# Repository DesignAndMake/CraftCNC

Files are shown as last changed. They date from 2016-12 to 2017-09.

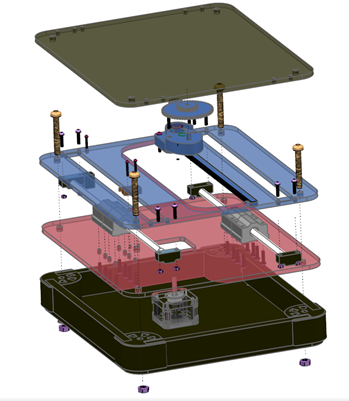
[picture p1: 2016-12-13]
CraftCNC_D1/Documentation/Assembly_Instructions/Images/Graphics/x axis 1.png

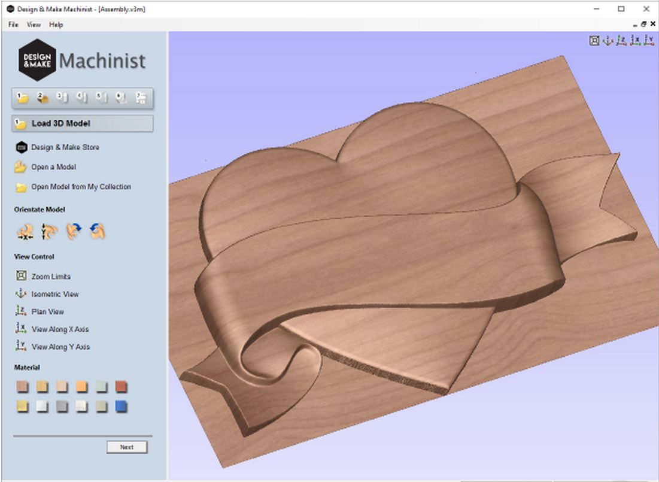
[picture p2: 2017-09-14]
CraftCNC_D1/Documentation/Assembly_Instructions/Images/Graphics/D&M Machinist.JPG

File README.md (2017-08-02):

## Welcome to the CraftCNC Wiki ##

If you want to build your own machine follow these steps:

* Download and print the STL files [STL files](https://github.com/DesignAndMake/CraftCNC/wiki/STL-files)
* Download and laser cut the DXF files [DXF files](https://github.com/DesignAndMake/CraftCNC/wiki/DXF-files-10mm)
* Follow the [Assembly Instructions](https://github.com/DesignAndMake/CraftCNC/wiki/Assembly-Instructions)
* Download and install the control software
* Grab a project from [Design & Make](https://www.designandmake.com)
* Your off!

## Self-build CNC

Self-build CNC (https://youtu.be/Zaxm20WJti4)

...more projects to follow

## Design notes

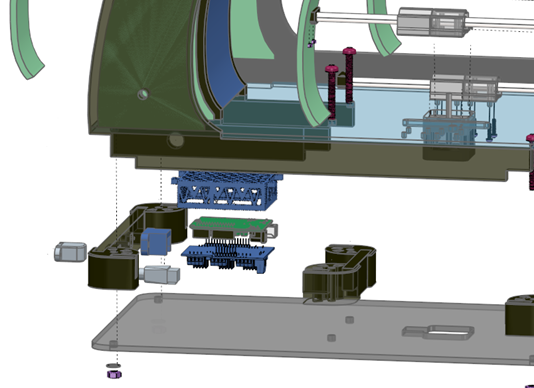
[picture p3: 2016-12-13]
CraftCNC_D1/Documentation/Assembly_Instructions/Images/Graphics/electronics 2.png

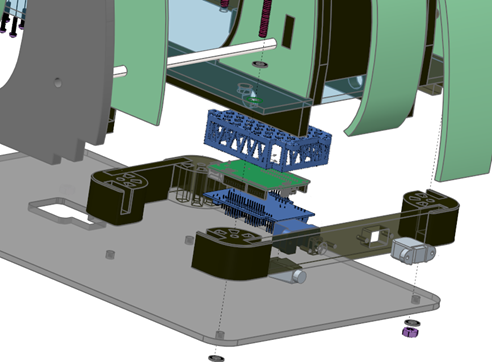
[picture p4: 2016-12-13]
CraftCNC_D1/Documentation/Assembly_Instructions/Images/Graphics/electronics 1.png

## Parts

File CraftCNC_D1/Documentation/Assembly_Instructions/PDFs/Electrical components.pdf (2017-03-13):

Image of electrical components | Description | Qty
| Emergency stop button | 1
| USB B to B connection | 1
| Limit switches | 3
| Solderless socket | 1

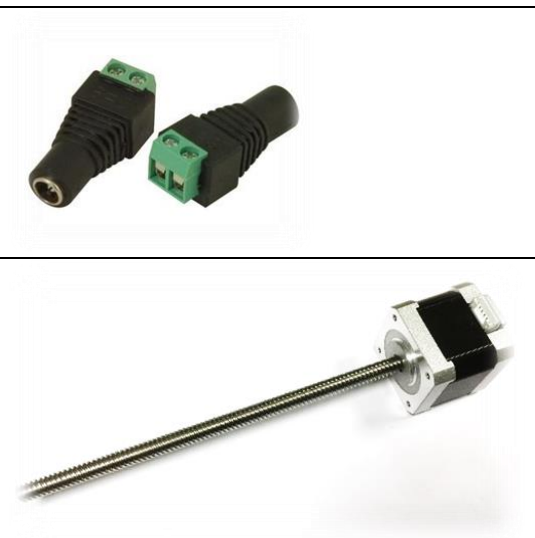
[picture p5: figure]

| Solderless socket 2 Alternative power socket. Use Either this socket or the one above. Both are NOT required | 1
| Nema 17, 42x40x40, stepper motors with integral ballscrew | 1

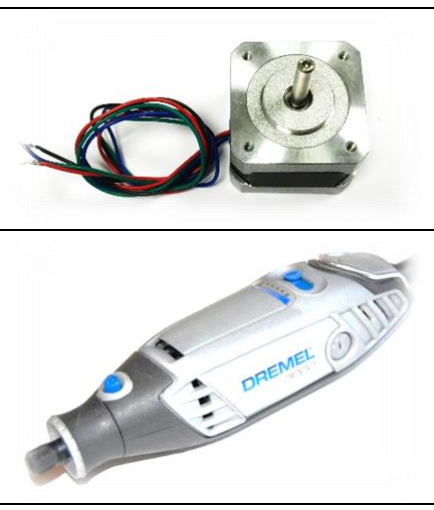
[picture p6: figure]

| Nema 17, 34x40x40, 0.9 mictostep | 2
| Dremel 3000 | 1

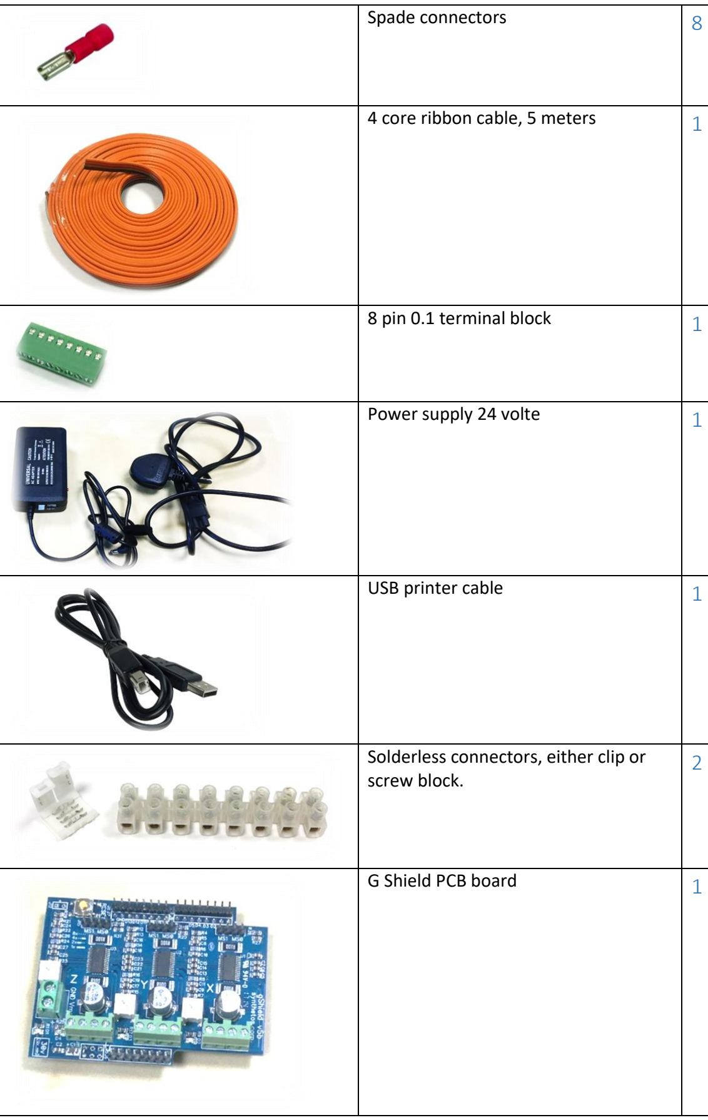
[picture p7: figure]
Spade connectors; 4 core ribbon cable, 5 meters; 8 pin 0.1 terminal block; Power supply 24 volte; USB printer cable; G Shield PCB board

Solderless connectors, either clip or screw block. | 2

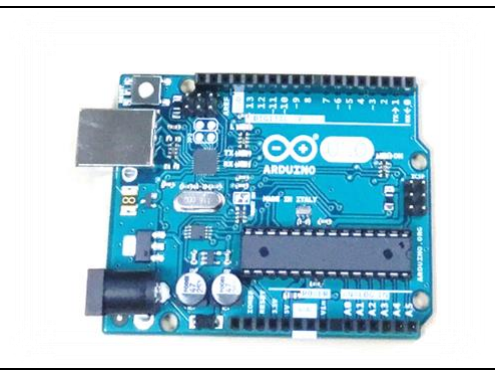
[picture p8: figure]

Arduino Uno PCB board | 1

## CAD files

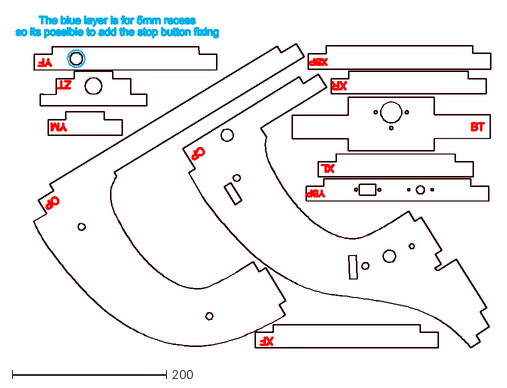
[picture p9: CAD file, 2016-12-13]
CraftCNC_D1/Hardware/DXF infromation/D1 10mm sheet/D1 10MM Material layer1.dxf
614.7 x 429.8

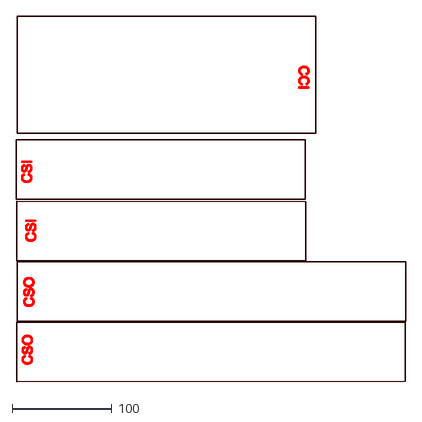
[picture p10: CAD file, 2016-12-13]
CraftCNC_D1/Hardware/DXF infromation/D1 3mm sheet/D1 3mm sheet layer 3.dxf
391.2 x 366.9

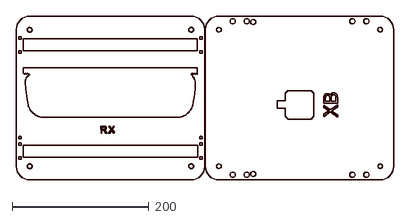
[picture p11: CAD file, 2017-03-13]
CraftCNC_D1/Hardware/DXF infromation/D1 5mm sheet/D1 5mm layer 3.dxf
553.0 x 240.0

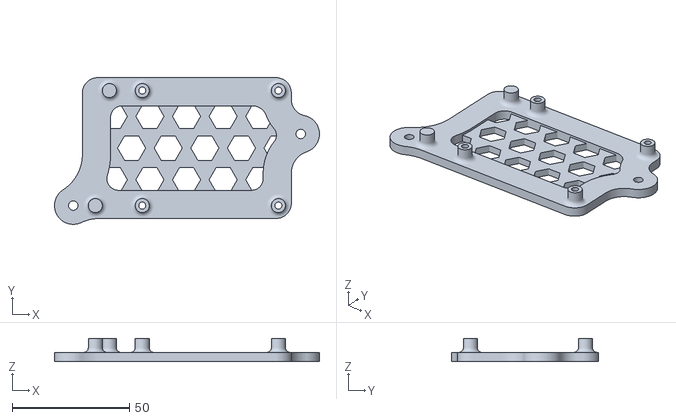
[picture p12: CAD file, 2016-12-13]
CraftCNC_D1/Hardware/STL infromation/D1 STL files/alternative components stls/pi holder.stl
112.9 x 62.5 x 10.0

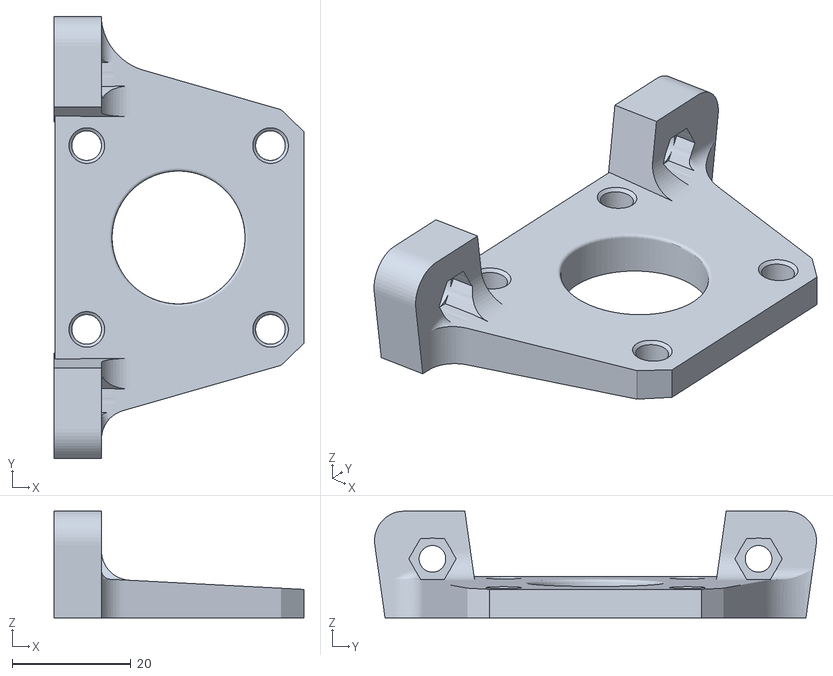
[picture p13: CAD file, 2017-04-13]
CraftCNC_D1/Hardware/STL infromation/D1 STL files/M&BS motor and baring support.stl
42.1 x 74.6 x 18.0

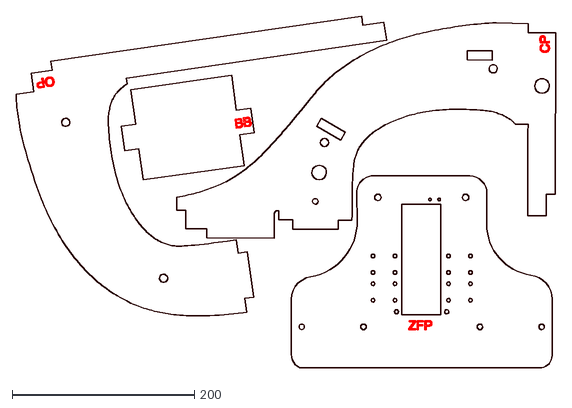
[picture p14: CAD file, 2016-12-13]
CraftCNC_D1/Hardware/DXF infromation/D1 10mm sheet/D1 10MM Material layer2.dxf
591.8 x 385.6

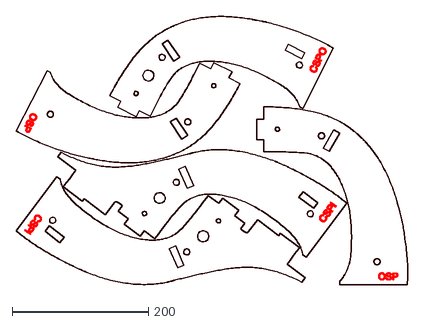
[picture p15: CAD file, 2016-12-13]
CraftCNC_D1/Hardware/DXF infromation/D1 3mm sheet/D1 3mm sheet layer 2.dxf
574.0 x 393.1

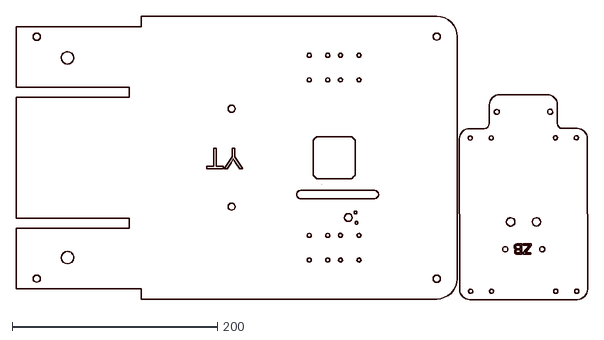
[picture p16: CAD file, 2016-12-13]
CraftCNC_D1/Hardware/DXF infromation/D1 5mm sheet/D1 5mm layer 1.dxf
557.4 x 276.5

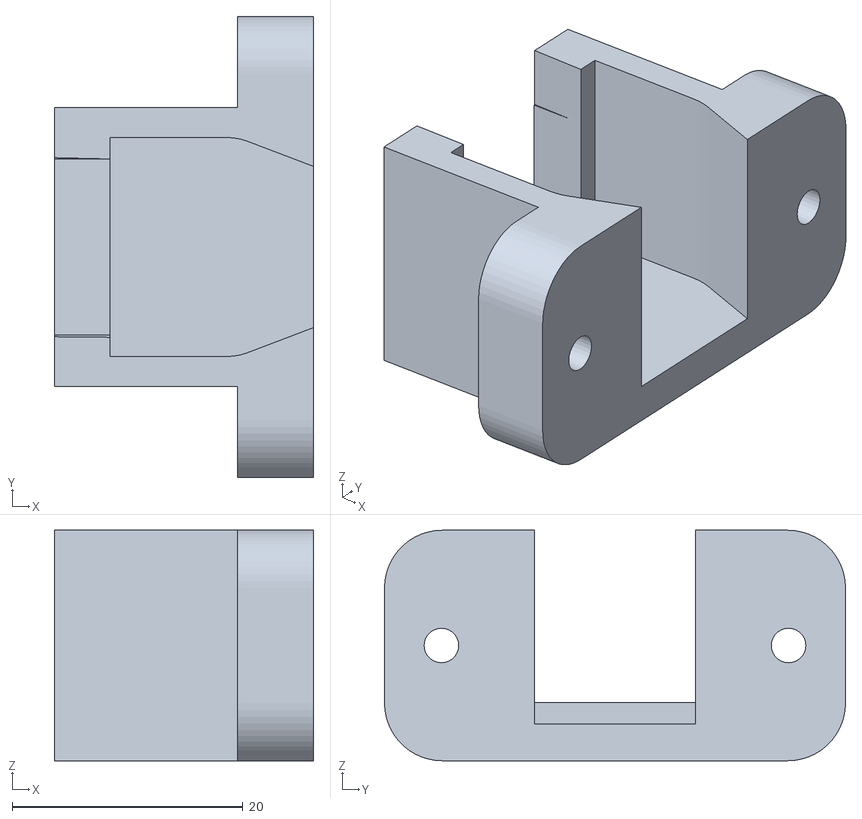
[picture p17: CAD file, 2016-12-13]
CraftCNC_D1/Hardware/STL infromation/D1 STL files/alternative components stls/power socket support.stl
22.5 x 40.0 x 20.0

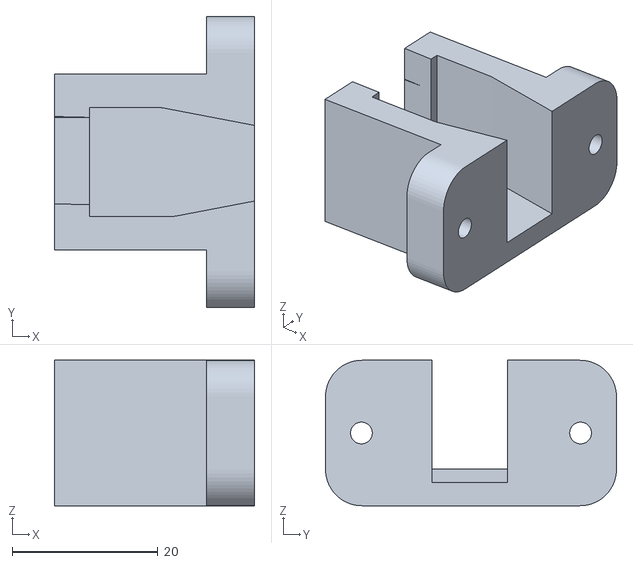
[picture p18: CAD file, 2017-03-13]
CraftCNC_D1/Hardware/STL infromation/D1 STL files/PS2 power socket support long.stl
27.5 x 40.0 x 20.0

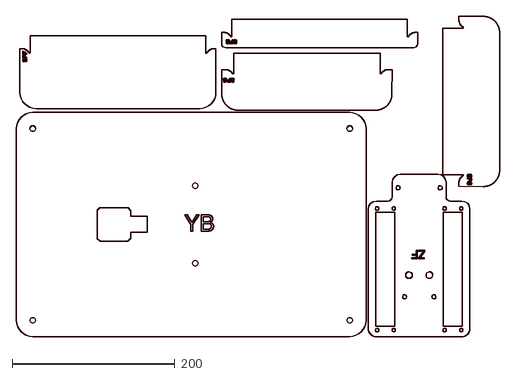
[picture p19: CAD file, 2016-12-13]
CraftCNC_D1/Hardware/DXF infromation/D1 5mm sheet/D1 5mm layer 2.dxf
594.4 x 394.2

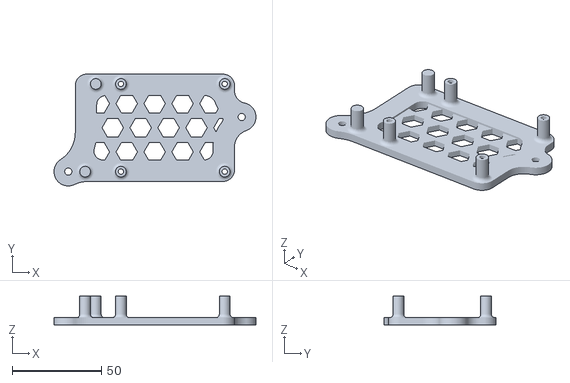
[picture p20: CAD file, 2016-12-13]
CraftCNC_D1/Hardware/STL infromation/D1 STL files/alternative components stls/protoneer holder.stl
112.9 x 62.5 x 16.0

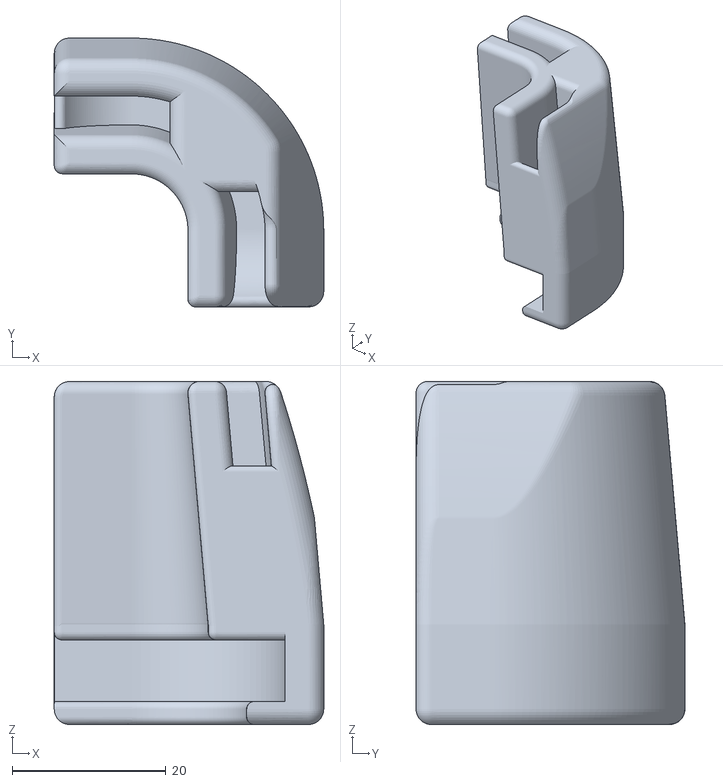
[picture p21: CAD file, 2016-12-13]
CraftCNC_D1/Hardware/STL infromation/D1 STL files/SGSL rear left safety guard bracket short.stl
35.1 x 35.0 x 44.6

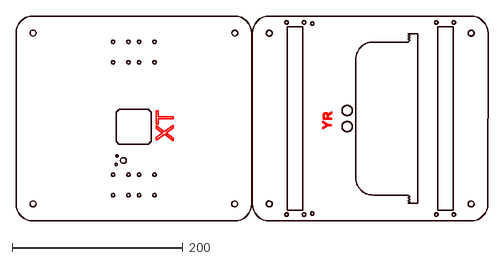
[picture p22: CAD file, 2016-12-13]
CraftCNC_D1/Hardware/DXF infromation/D1 5mm sheet/D1 5mm layer 4.dxf
553.0 x 240.0

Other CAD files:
CraftCNC_D1/Hardware/STL infromation/D1 STL files/alternative components stls/usb holder short.stl
CraftCNC_D1/Hardware/STL infromation/D1 STL files/SGSR rear right safety guard bracket short.stl
CraftCNC_D1/Hardware/STL infromation/D1 STL files/DG drive gear 58 tooth gear and 22 gear.stl
CraftCNC_D1/Hardware/STL infromation/D1 STL files/VO vacuum outer fitting.stl
CraftCNC_D1/Hardware/STL infromation/D1 STL files/BSC bearing support caps.stl
CraftCNC_D1/Hardware/STL infromation/D1 STL files/CS corner supports.stl
CraftCNC_D1/Hardware/STL infromation/D1 STL files/DBB dremel bottom bracket .stl
CraftCNC_D1/Hardware/STL infromation/D1 STL files/DTBA dremel holder top bracket adjuster.stl
CraftCNC_D1/Hardware/STL infromation/D1 STL files/DTBB dremel holder top bracket back.stl
CraftCNC_D1/Hardware/STL infromation/D1 STL files/DTBF dremel holder top bracket front .stl
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

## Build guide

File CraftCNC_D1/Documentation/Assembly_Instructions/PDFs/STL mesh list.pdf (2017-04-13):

Image of STL models | Description | Qty | weight | Density
| BSC Bearing support caps | 12 | 27.6 | 0.1mm z fine hatch
| CB Circuit board holder | 1 | 24.7 | 0.1mm z fine hatch
| CS Corner supports | 12 | 264 | 0.2mm z course hatch
| DBB Dremel bottom bracket | 1 | 23.7 | 0.15mm z Medium hatch
| DG Drive gear (58 tooth gear and 22 gear) | 2 | 18.4 | 0.1mm z fine hatch
| DTBA Dremel holder top bracket adjuster | 1 | 3 | 0.1mm z fine hatch
| DTBB Dremel holder top bracket back | 1 | 25.3 | 0.15mm z Medium hatch
| DTBF Dremel holder top bracket front | 1 | 16 | 0.15mm z Medium hatch
| GH Gear housing | 2 | 33 | 0.1mm z fine hatch
| LST Limit switch toggle | 2 | 3.2 | 0.15mm z Medium hatch

M&BS motor and baring support | 1 | 9.4 | 0.1mm z fine hatch
PCL Panel clip left | 1 | 18.7 | 0.15mm z Medium hatch

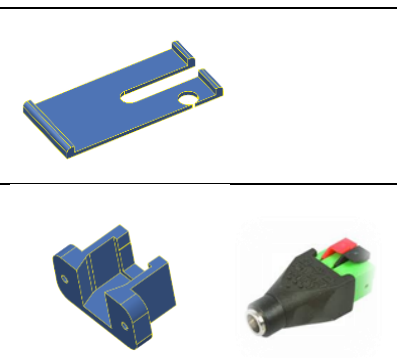
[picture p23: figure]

PCR Panel clip right | 1 | 18.7 | 0.15mm z Medium hatch
PS power socket support long | 1 | 7.3 | 0.15mm z Medium hatch
PS2 Alternative power socket 2 support long | 1 | 7.3 | 0.15mm z Medium hatch
SGS Corner safety guard supports | 2 | 83.4 | 0.2mm z course hatch
SGSL Rear left safety guard bracket short | 1 | 21.6 | 0.2mm z course hatch
SGSR Rear right safety guard bracket short | 1 | 21.6 | 0.2mm z course hatch
Vi Vacuum inner fitting | 1 | 18 | 0.15mm z Medium hatch
VO Vacuum outer fitting | 1 | 22 | 0.15mm z Medium hatch
XAR ‘X’axis rack | 1 | 8.8 | 0.1mm z fine hatch

YAR ‘Y’ axis rack | 1 | 9.8 | 0.1mm z fine hatch
ZASL ‘Z’ axis support left | 1 | 60 | 0.2mm z course hatch
ZASR ‘Z’ axis support right | 1 | 60 | 0.2mm z course hatch
ZBSH ‘Z’ axis ball screw holder | 1 | 13.8 | 0.1mm z fine hatch
ZK ‘Z’ axis knob | 1 | 6.6 | 0.15mm z Medium hatch

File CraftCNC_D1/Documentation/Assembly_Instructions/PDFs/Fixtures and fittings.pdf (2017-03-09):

Image of fixtures and fittings | Description | Qty
| M6 x 70mm roof bolts | 2

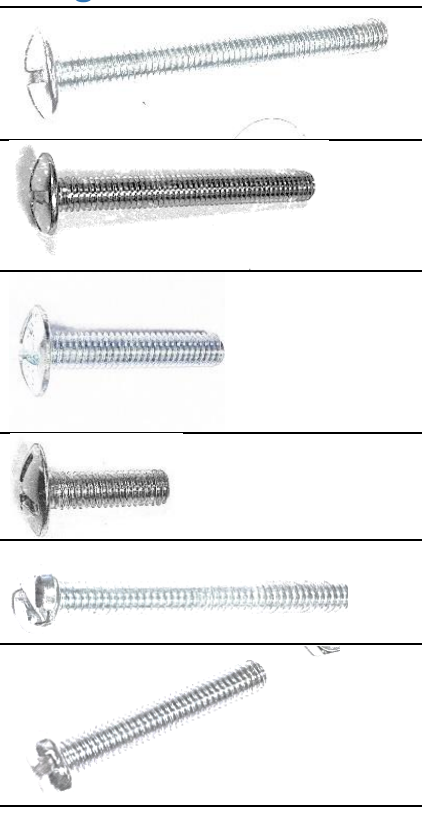
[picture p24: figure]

| M6 x 50mm roof bolts | 10
| M6 x 30mm roof bolts | 2
| M6 x 20mm roof bolts | 8
| M4 x 40mm bolts | 4
| M4 x 25mm bolts | 12

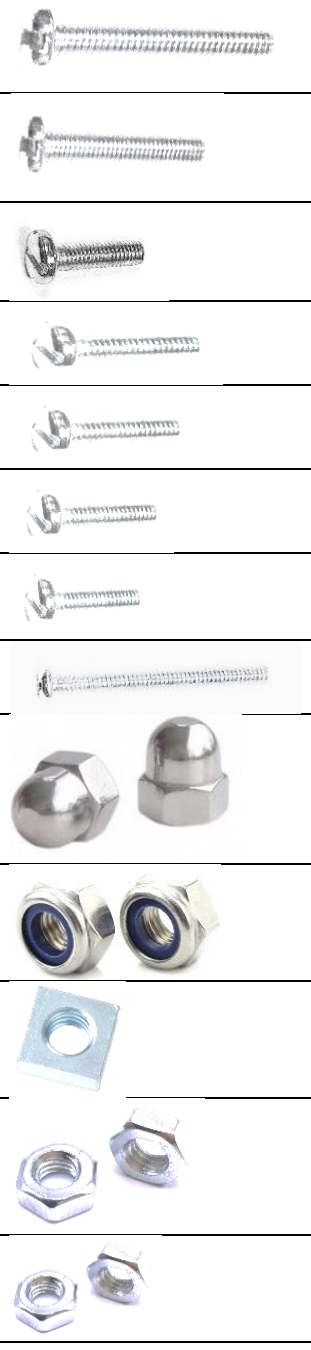
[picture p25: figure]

| M4 x 20mm bolts | 28
| M4 x 15mm bolts | 16
| M4 x 12mm bolts | 36
| M3 x 20mm bolts | 9
| M3 x 15mm bolts | 8
| M3 x 12mm bolts | 4
| M3 x 10mm bolts | 6
| M2 x 19mm bolts | 6
| M8 domed nuts | 4
| M6 hexagonal lock nuts | 6
| M6 square nuts | 16
| M4 Hexagonal nuts | 32
| M3 Hexagonal nuts | 31

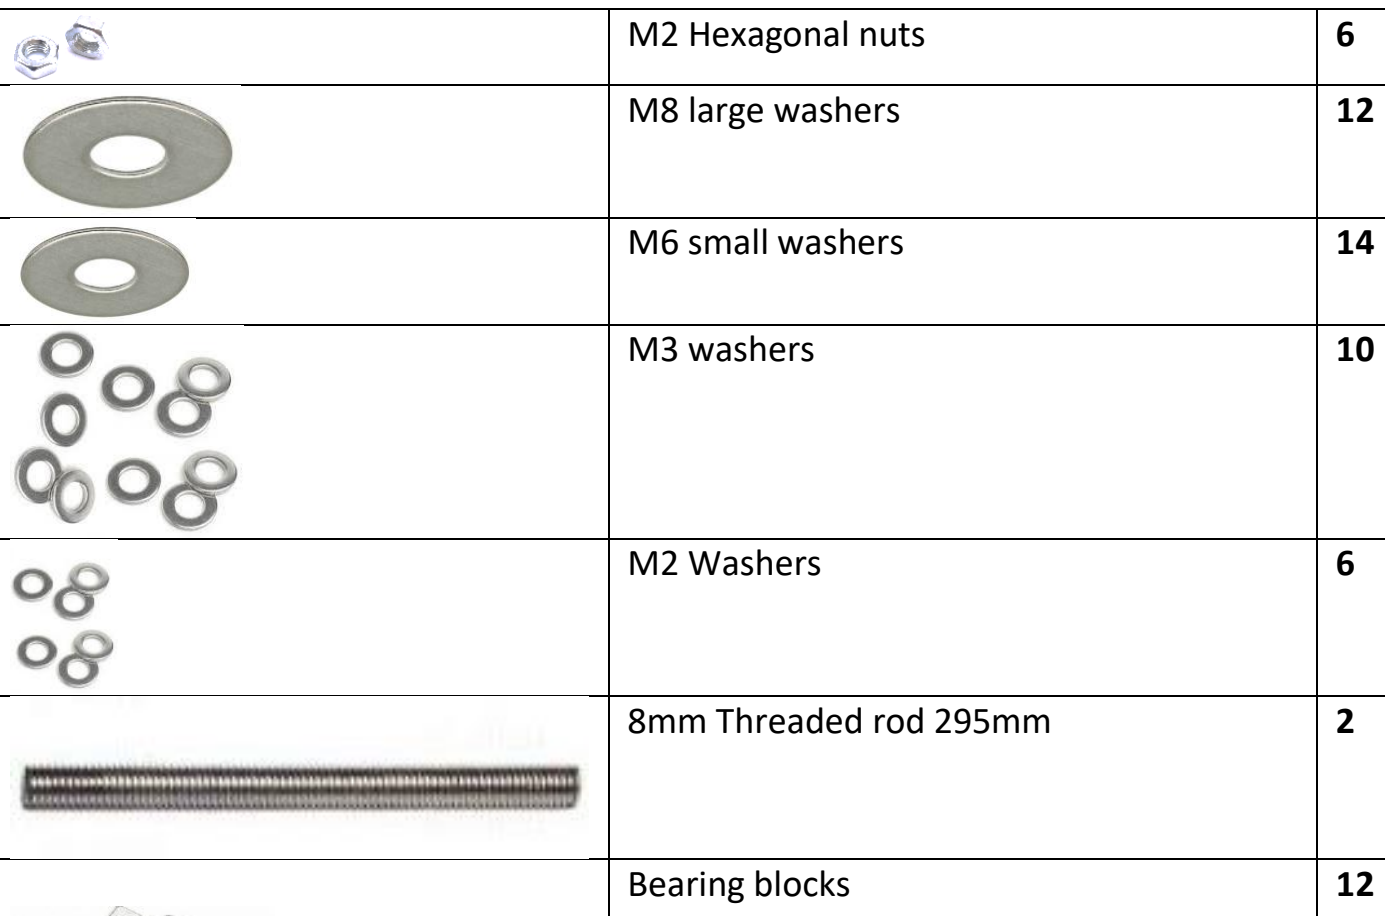
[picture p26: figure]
M2 Hexagonal nuts; M8 large washers; M6 small washers; M3 washers; M2 Washers; 8mm Threaded rod 295mm; Bearing blocks
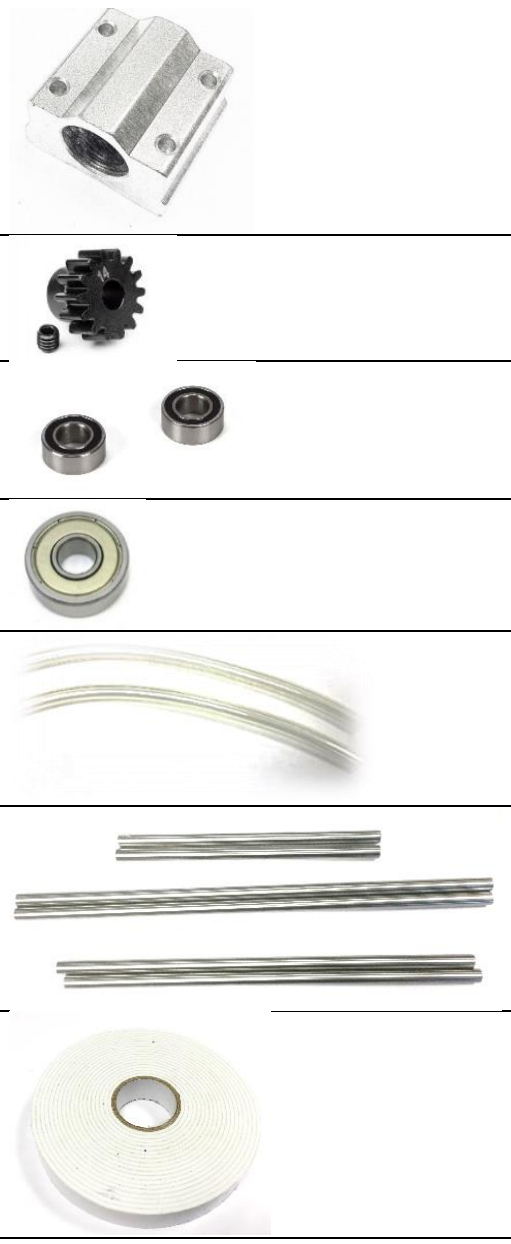
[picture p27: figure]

Pinion gear | 2
10mm bearings | 4
8x22x7 sealed bearing | 1
8mm vacuum tube 400mm | 2
8mm ground steel bars 2x150mm, 2x230mm and 2x270mm | 6
Roll of mounting tape | 1

PTFE glides for base of machine | 6

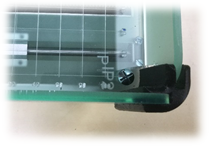
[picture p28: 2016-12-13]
CraftCNC_D1/Documentation/Assembly_Instructions/Images/Appendix_D/Fig D5.png

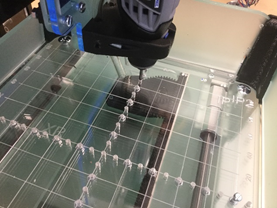
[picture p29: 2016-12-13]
CraftCNC_D1/Documentation/Assembly_Instructions/Images/Appendix_D/Fig D4.png

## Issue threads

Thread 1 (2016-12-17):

DXF files will not load into LibreCAD nor FreeCAD

dlarue, 2016-12-17:
I tried to determine the max sheet dimensions for our laser cutter but neither of my CAD programs can read the DXF files.  I can open DXF files from other projects without issue.

Looking at the downloaded file it appears to not be DXF file format but instead it's the Github view. ie the link is not pointing to the RAW data file.

If I go to github and get the raw data file(DXF format) it will open in LibreCAD and FreeCAD.

Baldricktrousers, 2016-12-17:
Hi Doug
If you right click over the Dfx file it should offer you the option to save as target file.
From the drop down, Select dxf and save to your pc this should then open correctly.

Let me know if you have any issues and I will take another look

Hope this helps

Baldricktrousers, 2016-12-17:
Hi Doug
Thanks for the info.
The dimensions for the laser are based on 600x400mm bed size
Hope this helps.

dlarue, 2016-12-17:
Both Firefox and Chromium do the same and download the html as if you just clicked on that link which gets you to the file viewing page on github.

For example, the link you have gets me here:
https://github.com/DesignAndMake/CraftCNC/blob/master/CraftCNC_D1/Hardware/DXF%20infromation/D1%2010mm%20sheet/D1%2010MM%20Material%20layer1.dxf

But it should be getting me here(notice raw at the beginning of the URL):
https://raw.githubusercontent.com/DesignAndMake/CraftCNC/master/CraftCNC_D1/Hardware/DXF%20infromation/D1%2010mm%20sheet/D1%2010MM%20Material%20layer1.dxf

Our laser cutter is 500mm x 300mm so it looks like we'll be splitting up moving parts around. But the biggest part still should just fit.

Baldricktrousers, 2016-12-18:
Hi Doug
Thanks for the update , we will change this as suggested, and good  to hear the dxf should still fit your laser.
We will supply a 500x 300 laser option, for the acrylic components, as this could be very helpful for others too.
Thanks again.

Baldricktrousers, 2016-12-19:
Hi Doug
Changes to downloading of DXF files are done: let me know if these are all OK.
I have taken a look at reorganising the items for a 500x300 laser, however there are 2 items that are 304mm in size, so the laser will require this size cutting area for these two items. However all other items should fit on a 500x300. I have saved them as CVR files and you can download the Vectric Trial software, open the files and export as dxf, it is also possible to change the layout as you wish.

Hope this helps.

dlarue, 2016-12-19:
I tested the layer 1 of the 10mm sheet and the file came down perfectly. Thanks.

I had seen the 304mm parts and figure the 4mm can be shaved off without effect on strength and aesthetics.

Closed 2016-12-19.

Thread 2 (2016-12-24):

parts #11,#20 and #23 links from exploded  view( STL ) incorrect

dlarue, 2016-12-24:
Link #11 references( notice the "&" symbol ):
https://github.com/DesignAndMake/CraftCNC/wiki/STL-Images-and-downloads#mb&s-motor-and-baring-support

which should be:
https://github.com/DesignAndMake/CraftCNC/wiki/STL-Images-and-downloads#mbs-motor-and-baring-support

Links #20(XAR x axis rack), #23(ZASR Z axis support right) are INOP too.

Baldricktrousers, 2016-12-24:
Hi Doug
Thanks for the heads up.
All corrected.

Thanks again

Closed 2016-12-24.

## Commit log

2016-11-15 Added link to assembly intructions wiki to readme main page
2016-12-13 Updated images and added model files
    [BSC bearing support caps.stl, CS corner supports.stl, D1 10MM Material layer1.dxf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]
2016-12-20 Create Grbl ini
